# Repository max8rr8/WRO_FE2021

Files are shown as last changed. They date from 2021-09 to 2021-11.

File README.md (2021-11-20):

# White Storks, WRO FE Solution

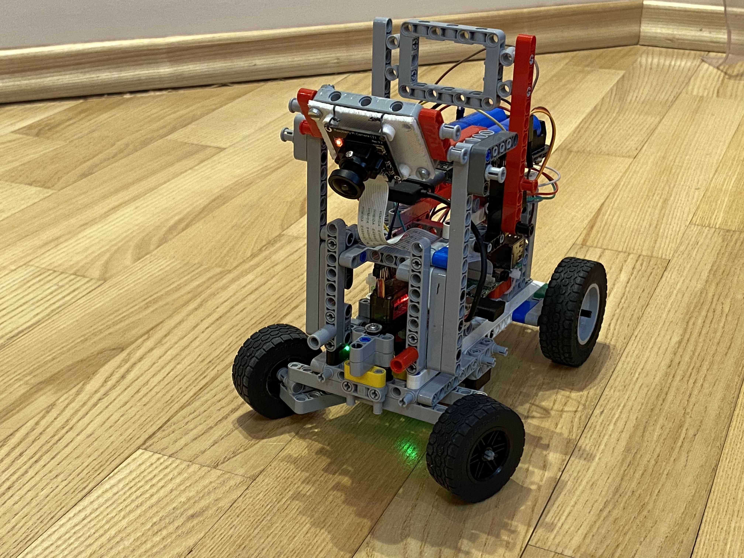
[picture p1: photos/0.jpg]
Image of robot


## Videos

### [Qualification round](https://youtu.be/TMEs1yODBv8)
### [Final round](https://youtu.be/N_jFORARUJI)

# Hardware

Our robot is made from following components:
* Main computer - Raspberry Pi 4 4GB
* 1х RPi Camera (I), Fisheye Lens, 170deg FOV
* 1x SD card 16Gb
* 1х Battery Shield V8
* 2x 18650 LiIon Batteries
* 1х DRV1.5DC, 1.5A 2 way DC Motor Driver Module PWM
* 1х JGA25-370 DC GEAR MOTOR 25GA-370 with Speed Encoder
* 1х Servo MG90S for steering 
* 1x Lego differential gears
* 1x Coupling 4 to 5 mm
* 2x Wheels Lego 62,4
* 1x Amperka Troyka Button
* 1x KY-016 RGB Full color led module
* 1x 3D printed camera mount, stl file is `cam_mount_v2.0.stl`

## Photos
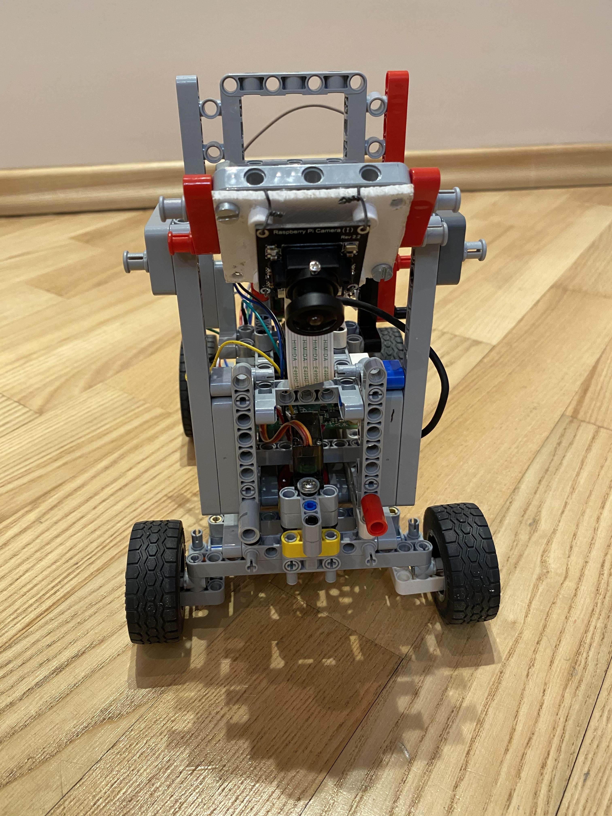
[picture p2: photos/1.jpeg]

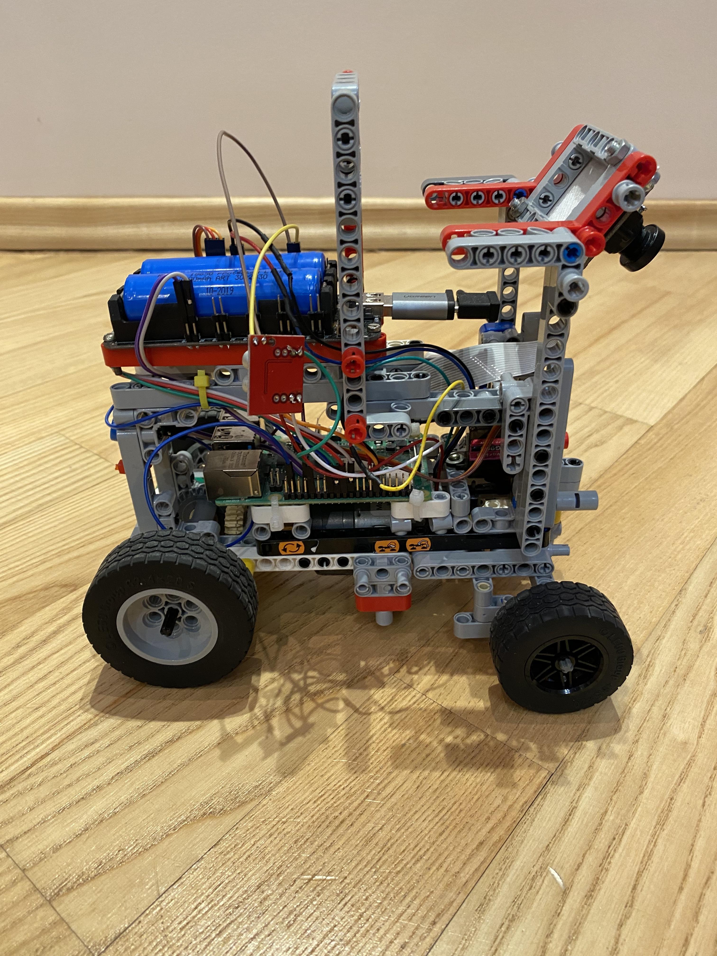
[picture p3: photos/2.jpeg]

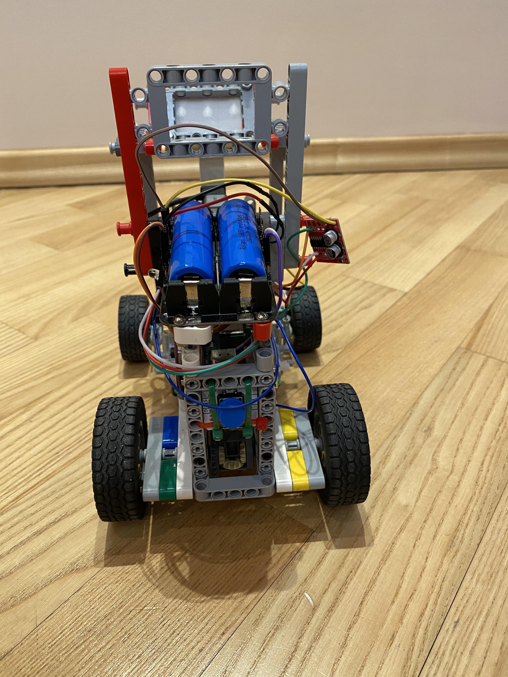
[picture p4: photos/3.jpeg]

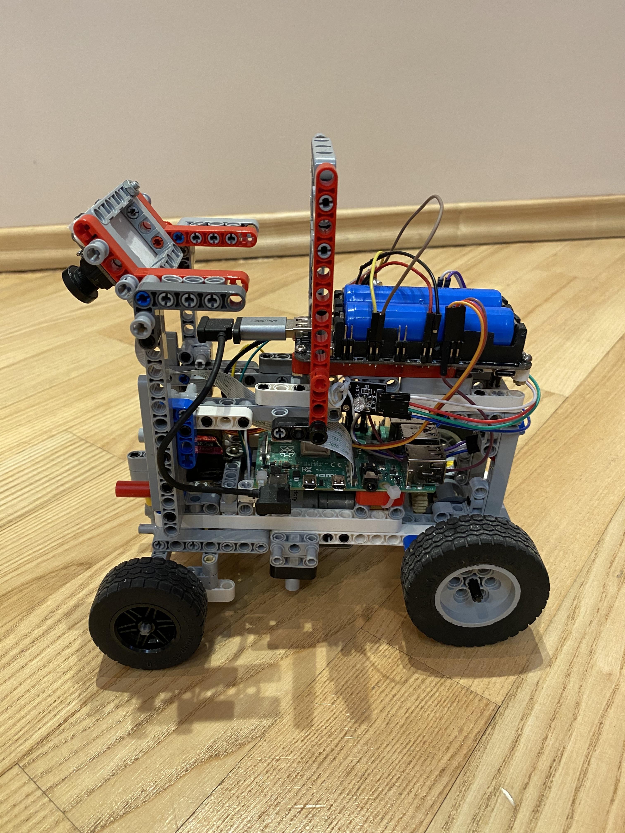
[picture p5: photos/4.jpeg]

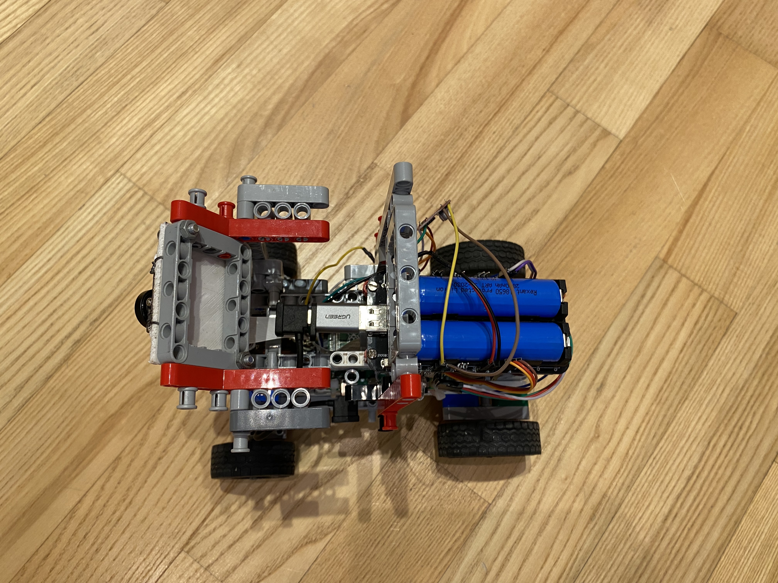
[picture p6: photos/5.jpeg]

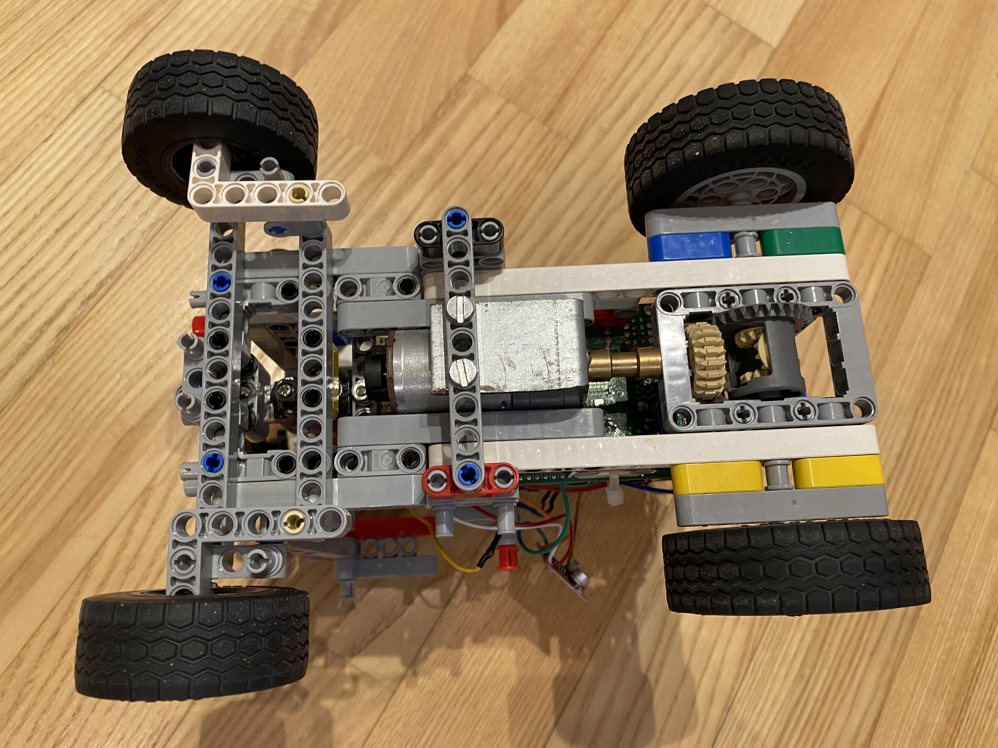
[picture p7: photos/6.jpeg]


## Schematics
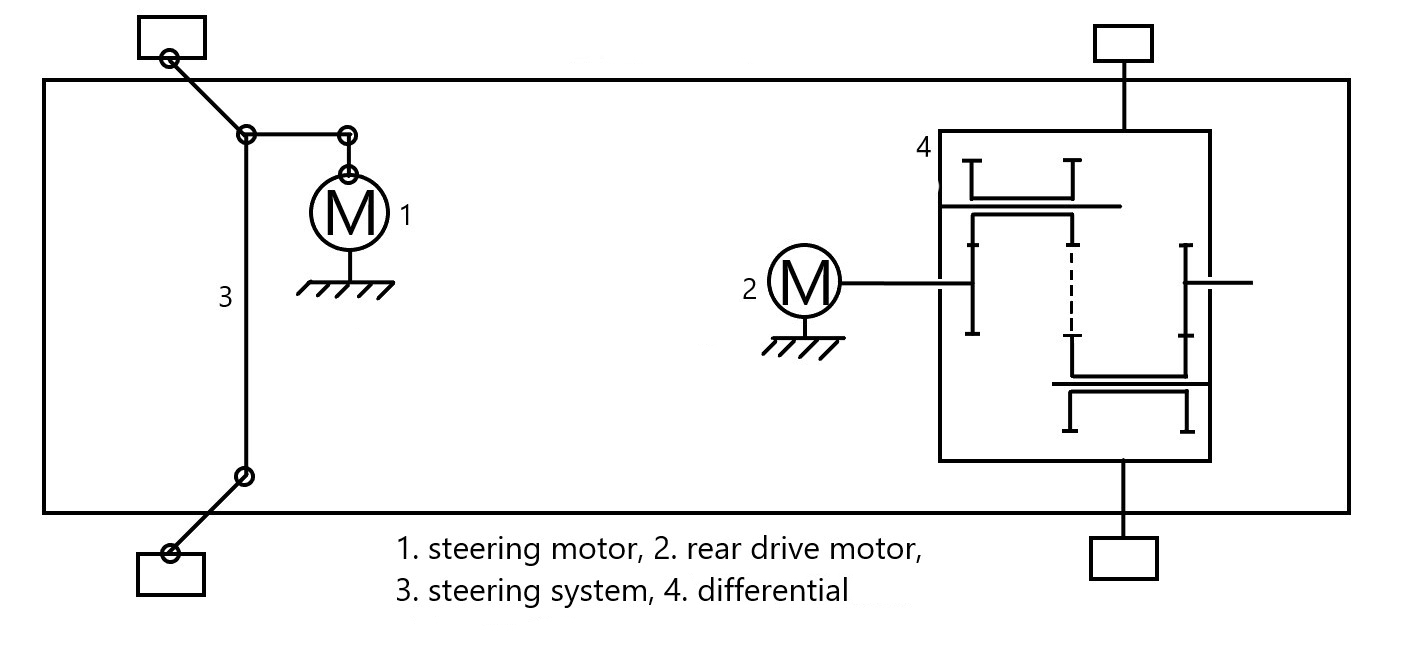
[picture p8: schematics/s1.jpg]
Schematics

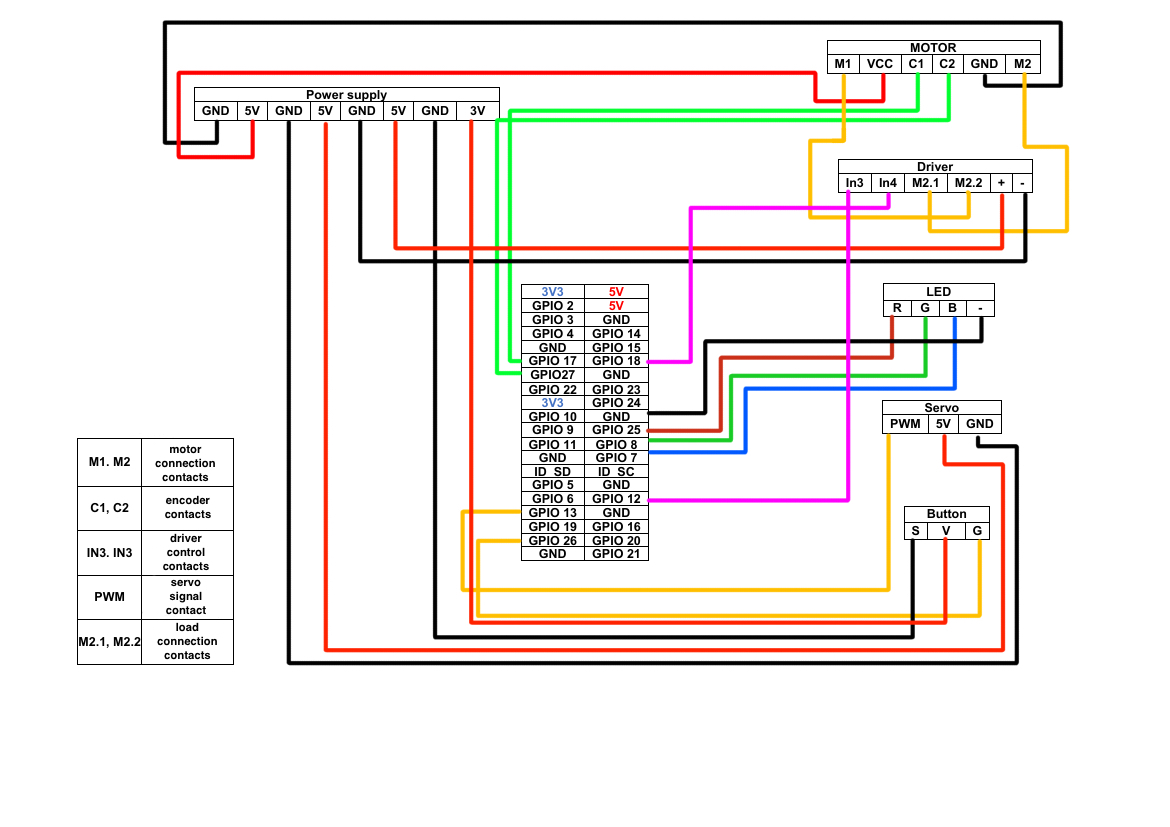
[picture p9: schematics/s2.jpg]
Electronics schematics


# Software

Components:

1. Main algorithm is done in `main.py`, [read more](#algorithm)
2. Configuration is done in files in `config` directory, [read more](#config)
3. Binarization and object detection, [read more](#object-detection)
4. There is smart algorithm for direction detection, [read more](#direction-detection).
5. Main movement algorithm is PID based on the distance from wall, [read more](#wall).
6. Markers detection is performed using hsv binarization and finding contours, [read more](#markers).
7. Lines are detected same way as markers, [read more](#turns-and-lines)
8. Turns is done using special "maneuver" algorithm, [read more](#turns-and-lines).
9. There is special program called `control.py` that helps with hsv binarization setup and hardware testing
10. Iterection with hardware done by code in `hardware` directory

## How to run 
1. Clone this repository
2. Install dependecies from `requirements.txt`
3. Run `sudo -E python3 ./main.py`

## Algorithm

Algorithm is implemented in `main.py`. There are two modes: Qualification and Final, configured in `config/config.py`.

Current sector in our terminology is number of turns since start

On start:

1. Detect direction [read more](#direction-detection).
2. Measure distance to wall([read more](#wall)) and remembered

Main loop in qualification mode:

1. If current sector is 0, 4, 8 or 12 then move along wall with distance that we measured in step 2 of start.
2. In other case move along wall with small distance, [read more](#wall).
3. If we are in sector 12 and encountered number of encoder ticks before finish sector, stop
4. If line(orange or blue) is detected ([read more][#turns-and-lines]) start turn, else go to step 1

Turn in qualification mode:

1. If this is first turn, record number of encoder ticks from start to line
2. If current sector is 4 or 8, record number of encoder ticks from line to line
3. If we are doing final turn, calculate ticks until finish using average of ticks from step 2 and subtract it by ticks from step 1
4. If we making turn before start sector (current sector is 3, 7 or 11), get maneuver based on direction of movement and distance from wall when we started from `QUALIFICATION_PRE_FINAL_MANEUVER`.
5. In other case get maneuver based on direction from `QUALIFICATION_MANEUVER`
6. Execute maneuver using `complex_maneuver`, [read more](#turns_and_lines)

Main loop in final mode:

1. Detect markers
2. Calculate how much we should change base wall point, depending on markers, [read more in wall](#wall).
3. Move along wall with calculated distance, [read more](#wall).
4. Also detect side markers(on next sector), so we do not need to detect when it is time to turn, [read more](#markers)
5. If we are in sector 12 and encountered number of encoder ticks before finish sector, stop
6. If line(orange or blue) is detected ([read more][#turns-and-lines]) start turn, else go to step 1

Turn in final mode:

1. Same as 1 step in qualification mode
2. Same as 2 step in qualification mode
3. Same as 3 step in qualification mode
4. Get last marker, if it was last seen more than 1 seconds ago consider there is no marker [markers](#markers)
5. Get filtered side marker, read more in [markers](#markers)
6. Get maneuver based on direction, last marker and current_marker, then execute it using `complex_maneuver`, [read more](#turns_and_lines)

## Config

To easily reconfigure our robot, we use files in `config` directory. Here is list of files with notes, what is stored inside configs:

- `config.py` - main config file, configures
  - Mode (qualification or final)
  - Wall movement
  - Values to shift wall point to bypass markers
  - Qualification sector detection
- `hardware.py` - configuration for hardware
  - Pins for motor, servo and led
  - Servo angles
  - Speed of movement
- `maneuver.py` - configuration for maneuvers (turns)
- `objects.py` - configuration for object detection
  - Side markers
  - Line (orange and blue)
  - Main markers

## Object detection

This section describes CV algorithms that we use for object detection, implementation `src/detection.py`.

First step is binarization of image, implemented in `binarize`:

1. Convert image to hsv
2. Check range for each pixel, if it is in range 255, otherwise 0, done via `cv2.inRange` binarization options are named `bin_min` and `bin_max` in all program files and configs.
3. Do four iterations of erosion, [read more](https://docs.opencv.org/master/d4/d86/group__imgproc__filter.html#gaeb1e0c1033e3f6b891a25d0511362aeb), used for noise removal.
4. Do four iterations of dilation, [read more](https://docs.opencv.org/master/d4/d86/group__imgproc__filter.html#ga4ff0f3318642c4f469d0e11f242f3b6c), used for noise removal.

Main detection algorithm, implemented in `detect_object`:

1. Crop image according to `zone` parameter, this name is used in all program files and configs.
2. Binarize cropped image
3. Find contours using `cv2.findContours` [read more](https://docs.opencv.org/master/d3/dc0/group__imgproc__shape.html#gadf1ad6a0b82947fa1fe3c3d497f260e0)
4. Remove contours with areas smaller than `area_min` (this name is used in all program files and configs), if there is no left return `(None, (None, None, None))`
5. Get biggest contour, calculate area and center
6. Return `(contoruPoints, (area, centerX, centerY))`
   This function also displays debug image, which is binarized image with maked contours:

- 1px green contour, contour detected but area is too small
- 3px green contour, contour detected but it is not biggest
- 3px red contour, contour is detected and it is biggest (returned)

## Dierction detection
UNDOCUMENTED, check file `src/direction.py`

## Wall

Wall detection and movement algorithms, implemented in `src/wall.py`

Algorithm for wall search is following, implemented in function `find_wall`:

1. Crop image by y coordinate based on config `WALL_SEARCH_Y`
2. If direction is clockwise get first `WALL_SEARCH_X` rows, else last `WALL_SEARCH_X` rows
3. Binarizae using same algorithm as used in [markers](#markers) with bin values from `WALL_BIN` config
4. For each row calculate last white pixel
5. Get average of them
   Wall search creates debug image, which is binarized image with green line showing average point

There is helper function `calculate_point` used in step 2 of main loop in final mode:

- If direction is clockwise return base_point + delta_point
- If direction is counterclockwise return base_point - delta_point

Main wall movement algorithm, implemented in function `wall`:

1. Detect wall using algorithm above
2. Calculate error subtracting target point from value we get in step 1
3. Calculate PD controller, and get correction
4. If we are moving counterclockwise inverse correction
5. Steer servo using correction

And there is another helper, which finds wall for 5 times and caclculates average of them, used in step 2 of on startup of main algorithm.

## Markers

Description of functions used for markers detection and processing. Implemented in `src/marker.py`

- `detect_side_markers` - Use object detection algorithm to detect side markers. In clockwise direction detected only red marker, in counterclockwise direction detected only green marker. Configuration for detection is in `SIDE_RED` and `SIDE_GREEN` in `config/objects.py`
- `find_side_markers` - Detect side markers and pushes it into queue with lenght 3, queue is used for error reduction. This method is used in step 4 of main loop in final mode.
- `get_side_markers` - Get side markers from queue(not modified). Returns most often seen.
- `detect_main_marker` - Detects main markers (just in one function). Configuration for detection is in `RED_MARKER` and `GREEN_MARKER` in `config/objects.py`
- `find_main_marker` - Run main markers detection. Then convert detecion result to one of `MARKER_NONE`, `MARKER_RED`, `MARKER_GREEN`, also writes time marker was seen and what was it. Used in step 1 of main loop in final mode.
- `get_last_marker` - If marker was seen less than 1 second ago return it, otherwise return `MARKER_NONE`. Used in step 4 of turn in final mode.
- `led_marker` - Set led color baed on marker seen, [read about led colors](#led).

## Turns and lines

We start turn if we detect orange or blue line, detection is implemented in `src/rotate.py`. This file contains function `should_start_rotate` whcih detects line, and checks if cooldown passed, then it return `True`, otherwise return `False`. Cooldown for line detection is 2 seconds.

Turn maneuvers are implemented in `src/maneuver.py`. There are two functions:

- `maneuver` - Simple maneuver, steers servo to given angle, and waits for encoder ticks
- `complex_maneuver` - Consists of two maneuvers, first move forward for given ticks(first argument), and then run second maneuver for given ticks and angle(second and third arguments)

# Team photos

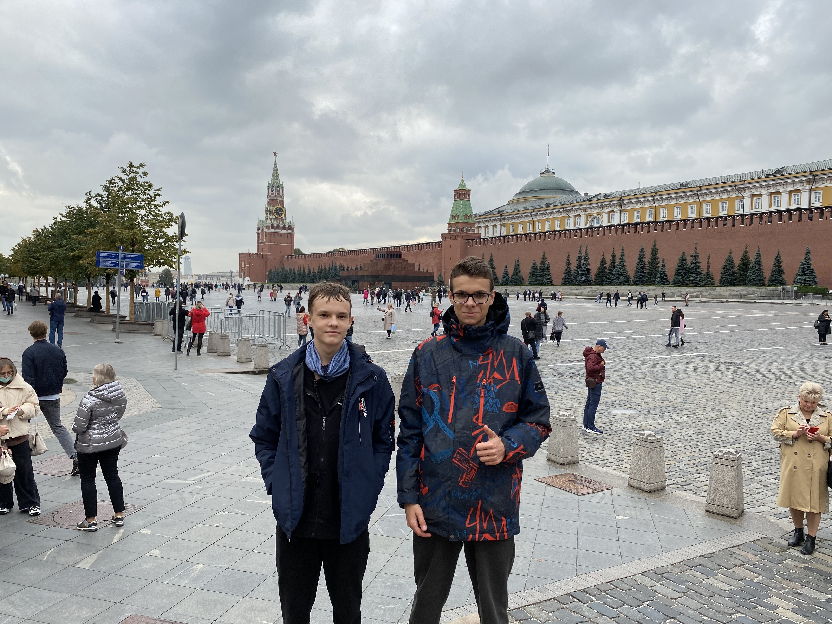
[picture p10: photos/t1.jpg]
Team 1

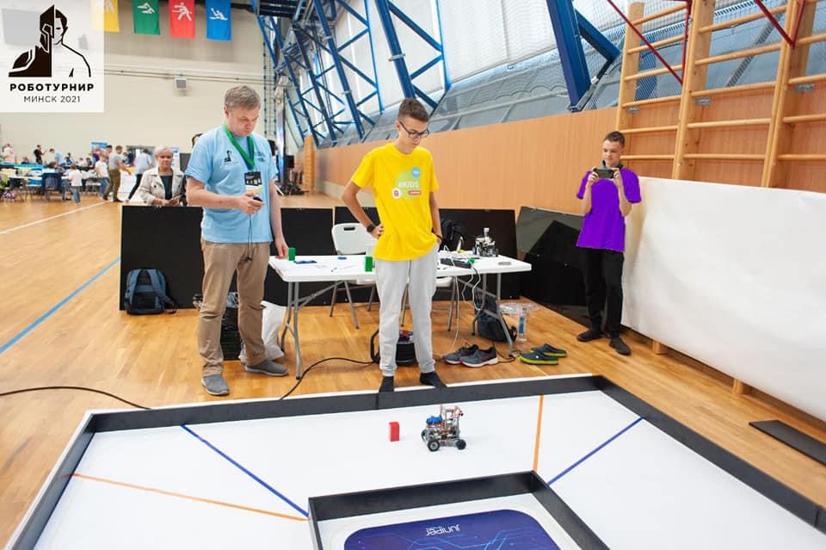
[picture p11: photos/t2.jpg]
Team 2


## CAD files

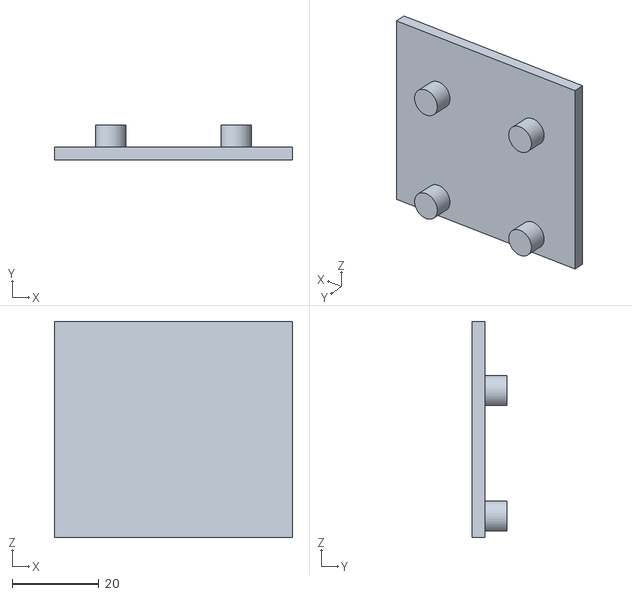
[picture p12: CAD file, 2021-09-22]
models/cam_mount_v2.0.stl
55.0 x 8.00 x 50.0

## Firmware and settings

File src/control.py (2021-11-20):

import cv2
import numpy as np
import hardware

AUTOHSV_MARGIN = 10

hardware.stop_center()

cv2.namedWindow("Control")


def draw_text(img, text, x, y, color=(255, 255, 255)):
  textsize = cv2.getTextSize(text, cv2.FONT_HERSHEY_PLAIN, 2, 2)[0]
  textX = int(x - textsize[0] / 2)
  textY = int(y + textsize[1] / 2)

  cv2.putText(img, text, (textX, textY), cv2.FONT_HERSHEY_PLAIN, 2, color, 2)


steer_status = "STOP"


def draw_steer_control():
  img = np.zeros((100, 480, 3))

  p = 80

  c = (0, 0, 255)
  if steer_status == "Forward": c = (0, 255, 0)
  if steer_status == "Reverse": c = (255, 0, 0)

  for text in ["Reverse", "STOP", "Forward"]:
    text_collor = c if text == steer_status else (255, 255, 255)
    draw_text(img, text, p, 50, color=text_collor)

    p += 160

    if p < 480:
      cv2.line(img, (p - 80, 0), (p - 80, 100), c, 2)

  cv2.imshow("Control", img)


def set_steer_control(event, x, y, flags, param):
  global steer_status
  if event == cv2.EVENT_LBUTTONDOWN:
    if x < 160:
      steer_status = "Reverse"
    elif x < 320:
      steer_status = "STOP"
    else:
      steer_status = "Forward"


cv2.setMouseCallback("Control", set_steer_control)

cv2.createTrackbar("Angle", "Control", 0, 100, lambda x: x)
cv2.setTrackbarPos("Angle", "Control", 50)

#############
detection_params = {
    "x1": 0,
    "y1": 0,
    "x2": 512,
    "y2": 384,
    "h_min": 0,
    "s_min": 0,
    "v_min": 0,
    "h_max": 255,
    "s_max": 255,
    "v_max": 255,
    "area_min": 300
}

cv2.imshow("Detection", np.zeros((1, 640)))


def creat_trackbar(param, val):
  max_val = 255
  if param[0] == "x": max_val = 512
  if param[0] == "y": max_val = 384
  if param == "area_min": max_val = 10000

  def change(x):
    detection_params[param] = x

  cv2.createTrackbar(param, "Detection", 0, max_val, change)
  cv2.setTrackbarPos(param, "Detection", int(val))


def binarize(img, bin_min, bin_max):
  hsv = cv2.cvtColor(img, cv2.COLOR_BGR2HSV)
  
  hsv[:, :, 0][hsv[:, :, 0] > 170] = 0
  bin_image = cv2.inRange(hsv, bin_min, bin_max)
  bin_image = cv2.erode(bin_image, None, iterations=4)
  bin_image = cv2.dilate(bin_image, None, iterations=4)

  return bin_image


def get_contour_params(cnt):
  M = cv2.moments(cnt)
  area = M['m00']
  cx = int(M['m10'] / area)
  cy = int(M['m01'] / area)

  return area, cx, cy


def detect_object(name, img, bin_min, bin_max, area_min):
  contour = None
  area, cx, cy = (None, None, None)

  binarized = binarize(img, bin_min, bin_max)
  debug = cv2.cvtColor(binarized, cv2.COLOR_GRAY2BGR)

  contours = cv2.findContours(binarized, cv2.RETR_TREE,
                              cv2.CHAIN_APPROX_NONE)[0]

  if len(contours) > 0:
    cv2.drawContours(debug, contours, -1, (0, 255, 0), 1)
    contours = list(filter(lambda c: cv2.contourArea(c) > area_min, contours))

    if len(contours) > 0:
      cv2.drawContours(debug, contours, -1, (0, 255, 0), 3)

      contour = max(contours, key=cv2.contourArea)
      area, cx, cy = get_contour_params(contour)

      cv2.drawContours(debug, [contour], -1, (0, 0, 255), 3)
      cv2.circle(debug, (cx, cy), 5, (0, 0, 255), -1)

  # cv2.imshow(name, debug)
  return contour, debug


cv2.namedWindow("Detection")

for param, val in detection_params.items():
  creat_trackbar(param, val)


def get_detection_params():
  return {
      "bin_min": (detection_params["h_min"], detection_params["s_min"],
                  detection_params["v_min"]),
      "bin_max": (detection_params["h_max"], detection_params["s_max"],
                  detection_params["v_max"]),
      "area_min":
      detection_params["area_min"]
  }


selecting_area = False
selecting_hsv = False

hsv_area = [(0, 0), (0, 0)]


def detection_buttons():
  img = np.zeros((80, 880, 3))

  p = 128

  c = (0, 255, 0)

  if selecting_area or selecting_hsv:
    draw_text(img, "Selectring AREA" if selecting_area else "Auto HSV", 512,
              40)
    img[78:80, :] = (0, 255, 0)
    return img.astype(np.uint8)

  for text in ["Select AREA", "Auto HSV", "Export", ""]:
    text_collor = (255, 255, 255)
    draw_text(img, text, p, 40, color=text_collor)

    p += 256

    if p < 880:
      cv2.line(img, (p - 128, 0), (p - 128, 128), c, 2)

  img[78:80, :] = (0, 255, 0)

  return img.astype(np.uint8)


def draw_detection_configuration():
  flag, img = hardware.get_frame(False)

  debug = np.zeros(img.shape, np.uint8)
  debug[:, :, 0] = 255

  try:
    cnt, det_debug = detect_object(
        "Detection", img[detection_params["y1"]:detection_params["y2"],
                         detection_params["x1"]:detection_params["x2"]],
        **get_detection_params())

    debug[detection_params["y1"]:detection_params["y2"],
          detection_params["x1"]:detection_params["x2"]] = det_debug

  except:
    print("Failed to detect object")

  cv2.rectangle(img, (detection_params["x1"], detection_params["y1"]),
                (detection_params["x2"], detection_params["y2"]), (0, 255, 0),
                2)

  if selecting_hsv:
    cv2.rectangle(img, hsv_area[0], hsv_area[1], (0, 0, 255), 2)

  img = cv2.hconcat([img, debug])
  buttons = detection_buttons()
  # print(img.shape, detection_buttons().shape)
  img = cv2.vconcat([buttons, img])

  cv2.imshow("Detection2", img)
  # cv2.imshow("Debug", debug)

cv2.namedWindow("Detection2")
selector_first_pressed = False


def autohsv(img):
  hsv = cv2.cvtColor(img, cv2.COLOR_BGR2HSV)

  h_min = max(np.min(hsv[:, :, 0]) - AUTOHSV_MARGIN, 0)
  s_min = max(np.min(hsv[:, :, 1]) - AUTOHSV_MARGIN, 0)
  v_min = max(np.min(hsv[:, :, 2]) - AUTOHSV_MARGIN, 0)

  h_max = min(np.max(hsv[:, :, 0]) + AUTOHSV_MARGIN, 255)
  s_max = min(np.max(hsv[:, :, 1]) + AUTOHSV_MARGIN, 255)
  v_max = min(np.max(hsv[:, :, 2]) + AUTOHSV_MARGIN, 255)

  cv2.setTrackbarPos("h_min", "Detection", h_min)
  cv2.setTrackbarPos("s_min", "Detection", s_min)
  cv2.setTrackbarPos("v_min", "Detection", v_min)
  cv2.setTrackbarPos("h_max", "Detection", h_max)
  cv2.setTrackbarPos("s_max", "Detection", s_max)
  cv2.setTrackbarPos("v_max", "Detection", v_max)


def export_detection():
  bin_min = (detection_params["h_min"], detection_params["s_min"],
             detection_params["v_min"])
  bin_max = (detection_params["h_max"], detection_params["s_max"],
             detection_params["v_max"])

  crop = f'(({detection_params["y1"]}, {detection_params["y2"]}), ({detection_params["x1"]}, {detection_params["x2"]}))'

  print(f"    'zone': {crop},")
  print(f"    'bin_min': {bin_min},")
  print(f"    'bin_max': {bin_max},")
  print(f"    'area_min': {detection_params['area_min']}")


def detection_button(event, x, y, flags, param):
  global selector_first_pressed
  global selecting_area
  global selecting_hsv
  global hsv_area
  
  if event == cv2.EVENT_LBUTTONDOWN:
    if y < 80:
      flag, img = hardware.get_frame(show=False)

      selector_first_pressed = False
      if x < 256:
        selecting_area = True
      elif x < 512:
        hsv_area = [(0,0),(0,0)]
        selecting_hsv = True
      else:
        export_detection()

    else:
      y -= 80
      if x < 512 and y > 0:
        selector_first_pressed = True

        if selecting_area:
          cv2.setTrackbarPos("x1", "Detection", x)
          cv2.setTrackbarPos("y1", "Detection", y)
        if selecting_hsv:
          hsv_area[0] = (x, y)

  elif event == cv2.EVENT_MOUSEMOVE:
    if selector_first_pressed:
      y -= 80
      if x < 512 and y > 0:
        if selecting_hsv:
          hsv_area[1] = (x, y)

        if selecting_area and x > detection_params[
            "x1"] and y > detection_params["y1"]:
          cv2.setTrackbarPos("x2", "Detection", x)
          cv2.setTrackbarPos("y2", "Detection", y)

  elif event == cv2.EVENT_LBUTTONUP:
    if selector_first_pressed:
      selecting_area = False

      if selecting_hsv:
        flag, img = hardware.get_frame(show=False)
        print(hsv_area)
        x1, y1 = hsv_area[0]
        x2, y2 = hsv_area[1]
        try:
          autohsv(img[y1:y2, x1:x2])
        except:
          pass
        selecting_hsv = False


cv2.setMouseCallback("Detection2", detection_button)

# cv2.createTrackbar("Detection", "x1", 0, 512, lambda x: x1)

while True:
  draw_steer_control()
  draw_detection_configuration()

  key = cv2.waitKey(1)

  if key == 27:
    break

  elif key == ord("w"):

    if steer_status == "STOP":
      steer_status = "Forward"
    elif steer_status == "Reverse":
      steer_status = "STOP"

  elif key == ord("s"):

    if steer_status == "STOP":
      steer_status = "Reverse"
    elif steer_status == "Forward":
      steer_status = "STOP"

  elif key == ord("a"):
    cv2.setTrackbarPos("Angle", "Control",
                       cv2.getTrackbarPos("Angle", "Control") - 25)

  elif key == ord("d"):
    cv2.setTrackbarPos("Angle", "Control",
                       cv2.getTrackbarPos("Angle", "Control") + 25)

  elif key == ord("e"):
    cv2.setTrackbarPos("Angle", "Control", 50)

  elif key == ord("q"):
    steer_status = "STOP"

  if steer_status == "STOP":
    hardware.set_direction(True)
    hardware.stop()
  elif steer_status == "Forward":
    hardware.set_direction(True)
    hardware.forward()
  elif steer_status == "Reverse":
    hardware.set_direction(False)
    hardware.stop()

  hardware.steer(cv2.getTrackbarPos("Angle", "Control") - 50)

  if key != -1:
    print(key, steer_status)

cv2.destroyAllWindows()

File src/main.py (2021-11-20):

from config.maneuver import QUALIFICATION_PRE_FINAL_MANEUVER
import cv2
import time
import hardware
from src.rotate import should_start_rotate
from src.maneuver import complex_maneuver
from src.wall import capture_wall, wall, calculate_point
from src.marker import get_count_markers, add_count_marker, is_left_marker, find_main_marker, find_side_markers, get_last_marker, get_side_markers, led_marker
from src.direction import find_direction  #, recognize_direction
from src.utils import report_start
from config import ENABLE_MOTORS, MANEUVERS, QUALIFICATION_SECTOR_BORDERS
from config import POINT_SHIFT, QUALIFICATION_MODE, WALL_POINT
from config import QUALIFICATION_WALL_POINT, QUALIFICATION_MANEUVER
from consts import MARKER_RED

######################################################################################
######################################################################################
######################################################################################

hardware.set_resolution(True)
report_start()
direction = find_direction()
hardware.set_resolution(False)

hardware.reset_encoder()
for i in range(7):
    hardware.get_frame()
    cv2.waitKey(10)

start_wall_point = capture_wall(direction)
print(start_wall_point)

current_sector = 0

start_ticks = hardware.read_encoder()
final_sector_ticks = 0
print("Direction:", direction, " Mode:", QUALIFICATION_MODE)

if ENABLE_MOTORS:
    hardware.forward(10)
    time.sleep(0.2)

last_left_seen = 0
count_of_markers = 0

final_sector = 11

roro = 0

while hardware.wait_button():
    start_time = time.time()
    flag, img = hardware.get_frame()
    # print(img.shape)

    if QUALIFICATION_MODE:
        hardware.led(0, 0, 1)
        wall(
            img, direction, (start_wall_point + 15) if current_sector == 0 else QUALIFICATION_WALL_POINT)

    else:
        marker = find_main_marker(img)


        if current_sector in [1,2,3,4] and is_left_marker(marker, direction):
            # print("SEEN", time.time() - last_left_seen)
            if time.time() - last_left_seen > 0.8:
                add_count_marker()

                cv2.imwrite(f"red{roro}.png", img)
                roro+=1
                print("DETECTED LEFT MARKER", get_count_markers(), time.time() - last_left_seen)

            last_left_seen = time.time()

        led_marker(marker)
        point_shift = POINT_SHIFT[marker]
        point = calculate_point(direction, start_wall_point if current_sector == 12 else WALL_POINT[direction], point_shift)
        # print("Marker", marker)
        wall(img, direction, point)

        find_side_markers(img, direction)

    if ENABLE_MOTORS:
        hardware.forward()

    if current_sector == final_sector + 1 and hardware.read_encoder() > til_finish_ticks:

        print("FINAL SECTORS", get_count_markers(), final_sector)
        hardware.stop_center()
        exit()

    if should_start_rotate(img, direction):
        hardware.led(1, 1, 1)

        if current_sector == 0:
            til_finish_ticks = hardware.read_encoder()
        elif current_sector == 4 or current_sector == 8:
            print("FINAL SECTOR TOOK", hardware.read_encoder())
            final_sector_ticks += hardware.read_encoder()
        elif current_sector == 7:
            print("FINAL SECTOR", get_count_markers())
            # final_sector += get_count_markers()
        elif current_sector == final_sector:
            print("FINAL SECTORS", get_count_markers())
            til_finish_ticks = 1100 # final_sector_ticks / 2 - til_finish_ticks - 260

        if QUALIFICATION_MODE:
            # if current_sector % 4 == 3:
            #     if start_wall_point > QUALIFICATION_SECTOR_BORDERS[1]:
            #         side_sector = -1
            #     elif start_wall_point < QUALIFICATION_SECTOR_BORDERS[0]:
            #         side_sector = +1
            #     else:
            #         side_sector = 0

            #     print("Executing qualification pre-final maneuver", direction, side_sector)

            #     complex_maneuver(*QUALIFICATION_PRE_FINAL_MANEUVER[direction][side_sector])
            # else:
            print("Executing qualification base maneuver", direction)
            complex_maneuver(*QUALIFICATION_MANEUVER[direction])
        else:
            last_marker = get_last_marker()
            side_marker = get_side_markers()


            print("Executing maneuver", direction, last_marker, side_marker)
            complex_maneuver(*MANEUVERS[direction][last_marker][side_marker])
            # hardware.stop_center()
            # exit()
            if side_marker == MARKER_RED:
                last_left_seen = time.time()

            if current_sector in [1,2,3,4] and side_marker == MARKER_RED:
                add_count_marker()
                flag, img = hardware.get_frame()
                cv2.imwrite(f"red{roro}.png", img)
                roro+=1

        current_sector += 1
        hardware.reset_encoder()

        img = None

        for i in range(10):
            a = hardware.get_frame()
            cv2.waitKey(1)
        # last_left_seen = time.time()
        # if current_sector == 1:
        #     exit(1)
    

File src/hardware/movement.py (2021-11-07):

from config.config import QUALIFICATION_MODE
from config.hardware import *
import RPi.GPIO as GPIO
import wiringpi
import time

wiringpi.pinMode(SERVO_PIN, wiringpi.GPIO.PWM_OUTPUT)
wiringpi.pinMode(MOTOR_PIN, wiringpi.GPIO.PWM_OUTPUT)

GPIO.setup(16, GPIO.OUT)
# GPIO.output(16, 0)
pwm = GPIO.PWM(16, 50)

wiringpi.pwmSetMode(wiringpi.GPIO.PWM_MODE_MS)
wiringpi.pwmSetClock(192)
wiringpi.pwmSetRange(2000)

wiringpi.pwmWrite(SERVO_PIN, 165)


def forward(speed=1):
    base_speed = QUALIFICATION_SPEED if QUALIFICATION_MODE else BASE_SPEED
    wiringpi.pwmWrite(MOTOR_PIN, int(base_speed * speed))


def stop():
    wiringpi.pwmWrite(MOTOR_PIN, 0)


def steer(angle):
    # print(angle)
    angle += CENTER_ANGLE

    # if angle < LEFT_ANGLE:
    #     angle = LEFT_ANGLE

    # if angle >= RIGHT_ANGLE:
    #     angle = RIGHT_ANGLE

    wiringpi.pwmWrite(SERVO_PIN, int(angle))


def stop_center():
    stop()
    steer(0)


def set_direction(direction):
    # pass
    if direction:
        pwm.stop()
    else:
        pwm.start(100)

def pause_for(seconds):
    stop_center()
    time.sleep(seconds)

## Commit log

2021-08-26 все работает кроме поворотов
2021-09-19 Some more refactor * Add led * Move hardware config to config * Add universal method to wait for button (both cv and real)
2021-09-22 Add docs
    [cam_mount_v2.0.stl]
2021-09-24 Add button for pre start
2021-11-07 Add schematics
